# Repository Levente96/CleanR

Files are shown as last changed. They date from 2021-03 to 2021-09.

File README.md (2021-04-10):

# CleanR
CleanR is a DIY air purifier project.

**Goal** of the project is to create an air purifier which is cheaper and more silent than the commercially available ones.

## Components
Current revision is based on the following components:
* NF-A14 industrialPPC-24V-3000 Q100 IP67 PWM
* Random HEPA filter(*should not matter as long as it works*)
* 3D printed case(*see resources*)
* USB-C power input
* DC-DC step-up module

## Assembly
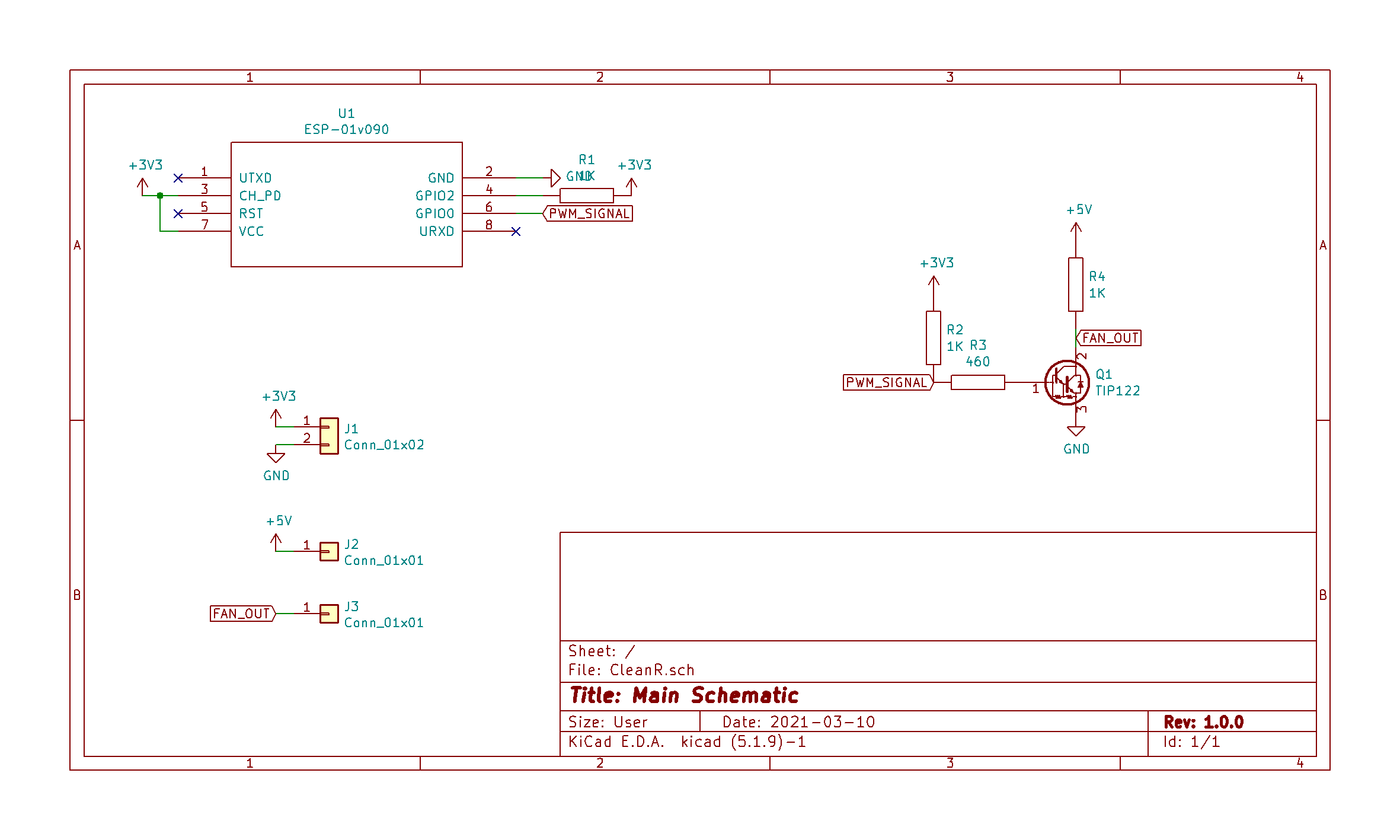
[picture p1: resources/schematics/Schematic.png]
schematic Schematic

For the filter, I found an [alternative](https://www.aliexpress.com/item/32861099829.html), which you should cut in half (alongside the longer side), so the filter will be 145mm "tall".
I have also attached strigs from the bottom to the fan's bottom screws to load the bottom up to the filer when lifted.

## Perforamnce
The goal is to beat the following performance:
> 320m^3/h (recommended for up to 106m^2) of air for ~100$ with 31-61dB(A)

Simplifying this means you got 3m^3/h for each m^2 which means you are paying '~1$/m^2'.
Our performance is the following:
> 260m^3/h (according to Noctua specs) with up to 41dB(A) of noise

Calculating the "optimal" m^2 for this device would be 86 m^2 which is still larger than I need, for around 1/3-rd of the cost.

This design is **2.59 times** more value ($/cleaned air) than the Xiaomi Air Purifier 3C.

## Cost
The goal of all time to keep the cost under ~100$. Currently it costs:

| Item | Cost |
| ---- | ---: |
| Fan  | 33$  |
| Filter | 3$ |
| DC Converter | 1$ |
| Connector + cables | <1$|
| 3D printed box | ~3$ |
| ESP-01 | 1$ |
| 1K ohm resistor| <1$ |
| TIP122 | <1$ |
| **Total:** | **42$** |

> **Note:** The development environment only works in linux with legacy dependencies, use it on a virtualbox.

## Roadmap
* `v1.0`: Simplest version, with no other optioans than plugged in and running, and poweroff state :heavy_check_mark:
* `v2.0`: ESP8266 built-in for controlling the fan-speed according to preprogrammed timestamps :heavy_check_mark:
* `v3.0`: ~ESP8266 with full IoT features inluding AWS integration and wireless access~ basic web interface :heavy_check_mark: , OTA :heavy_check_mark: , redesign :heavy_check_mark:
* `v4.0`: Mesh network of these devices with standalone air quality measurement point

## Resources
* [Noctua](https://noctua.at/en/nf-a14-industrialppc-24v-3000-q100-ip67-pwm)
* [Air purifier tests](https://smartairfilters.com/en/blog/xiaomi-purifier-auto-mode-leaves-air-unsafe-86-hours/)
* [Noctua PWM white paper](https://noctua.at/pub/media/wysiwyg/Noctua_PWM_specifications_white_paper.pdf)
* [ESP Tool](https://github.com/espressif/esptool)
* [Expressif FreeRTOS SDK](https://github.com/espressif/ESP8266_RTOS_SDK)
* [Expressif IDF](https://github.com/espressif/esp-idf)

---


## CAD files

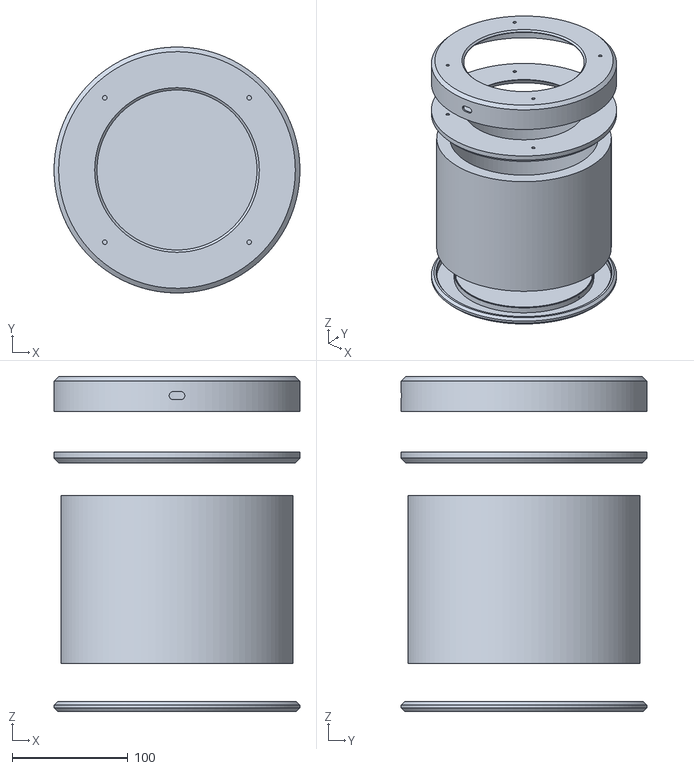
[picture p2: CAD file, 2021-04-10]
resources/mechanics/CleanRv2.stl
212.1 x 212.1 x 289.0

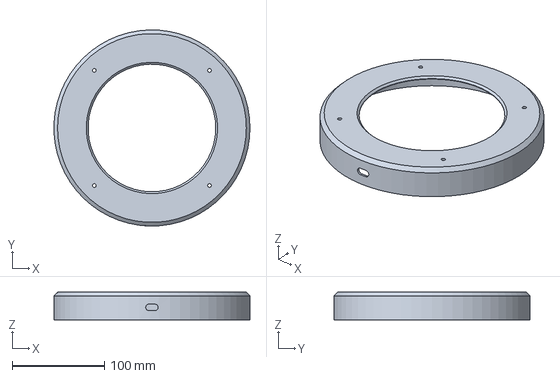
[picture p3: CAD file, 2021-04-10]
resources/mechanics/AirPurifier.FCStd
212.0 x 212.1 x 30.0 mm

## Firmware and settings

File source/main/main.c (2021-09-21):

#include "freertos/FreeRTOS.h"
#include "freertos/task.h"
#include "freertos/queue.h"

#include "esp_system.h"
#include "esp_log.h"
#include "esp_netif.h"
#include "esp_event.h"
#include "esp_err.h"
#include "nvs.h"
#include "nvs_flash.h"

// Component headers
#include "cleanr_http_server.h"
#include "cleanr_ota_service.h"

httpd_handle_t server = NULL;

void app_main()
{
    ESP_ERROR_CHECK(nvs_flash_init());
    ESP_ERROR_CHECK(esp_netif_init());
    ESP_ERROR_CHECK(esp_event_loop_create_default());

	xTaskCreate(&ota_task, "ota_task", 8192, NULL, 5, NULL);

    ESP_ERROR_CHECK(esp_event_handler_register(IP_EVENT, IP_EVENT_STA_GOT_IP, &connect_handler, &server));
    ESP_ERROR_CHECK(esp_event_handler_register(WIFI_EVENT, WIFI_EVENT_STA_DISCONNECTED, &disconnect_handler, &server));

    server = start_webserver();
	
}

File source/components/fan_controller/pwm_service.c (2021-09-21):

#include "pwm_service.h"

const uint32_t pwm_pin_num[1] 		= { PWM_FAN_OUT_IO_NUM };
uint32_t 	   pwm_duty_cycle_us[1] = { 23 };
float 	 	   pwm_phase_shift[1]   = { 0 };
uint8_t 	   pwm_fan_speed 		= 0;

void pwm_init_service()
{
	pwm_init(PWM_PERIOD_US, pwm_duty_cycle_us, 1, pwm_pin_num);
	pwm_set_phases(pwm_phase_shift);
	pwm_start();
	pwm_fan_speed = (uint8_t)((float)(pwm_duty_cycle_us[0] / PWM_PERIOD_US) * 100);
}

void pwm_set_fan_speed(uint8_t percent)
{
	if(percent > 100) percent = 100;
	
	pwm_duty_cycle_us[0] = (uint8_t)((float)(PWM_PERIOD_US / 100.0) * percent);
	pwm_fan_speed = percent;
	pwm_set_duties(pwm_duty_cycle_us);
}

void pwm_get_fan_speed(uint8_t* percent)
{
	//TODO
}

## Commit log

2021-03-02 Sketch version of the case
    [AirPurifier.FCStd, CleanR.stl]
2021-03-04 First version with fitting dimensions
    [AirPurifier.FCStd]
2021-03-04 Size update
    [AirPurifier.FCStd, CleanR.stl]
2021-03-05 v1.0 fitted, tested
    [AirPurifier.FCStd, CleanR.stl]
2021-03-10 Schematic added
    [CleanR.kicad_pcb, CleanR.sch]
2021-03-10 Structured contents
    [AirPurifier.FCStd, CleanR.stl]
2021-03-16 PWM service and http server update
2021-03-17 Schematic size
    [CleanR.sch]
2021-09-21 Refactor according to ESP guidelines
    [CleanRv2.stl]
